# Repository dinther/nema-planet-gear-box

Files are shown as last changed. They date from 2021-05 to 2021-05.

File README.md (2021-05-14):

# nema-planet-gear-box
parametric, silent planet gearbox for 3D print

# Introduction
Yes, yet another 3D printable planet gearbox. For my project I needed a gearbox as flat as I could possibly make it and silent. The result is this gearbox that can measure as thinas 8 mm thick depending on torque requirements and D-shaft design on the motor at hand. The gearbox is stackable where subsequent stacks are even thinner than the first one.

Contrairy to the many well intended 3D printable panet gear solutions out there, this gearbox is mathematically correct. What this means is that not all teeth combinations mesh properly. They can be forced to mesh by adjusting various tolerances but the result would be a wobbly and noisy gearbox. You know the ones.

This gearbox is tried, printed, modified, printed again tested over an over for months with a pile of parts to show for it. But the results are worth it as you can see in the linked video.

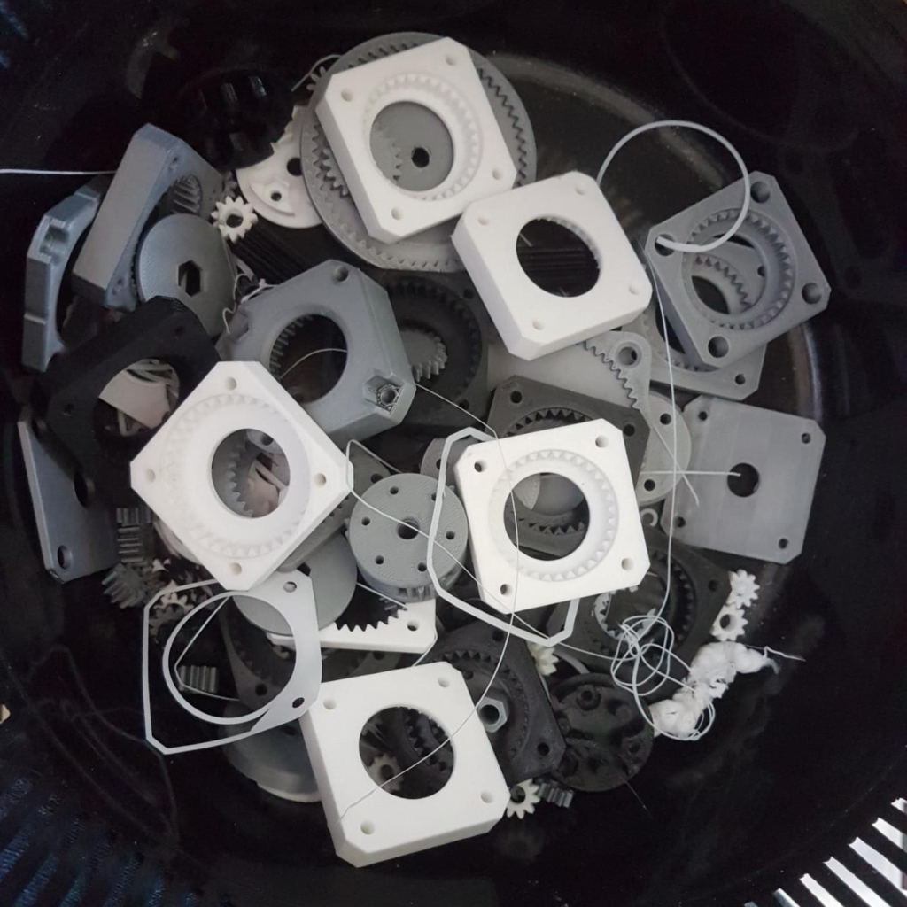
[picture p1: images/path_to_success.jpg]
Path to success

<video width="320" height="240" controls>
  <source src="nema17_quiet_gearbox.mp4" type="video/mp4">
</video>

# Capabilities
This planet gearbox comes in four sizes to match Nema11, Nema14, Nema17, Nema23 and Nema34. It uses 3 planet gears driven by the sun gear in the middle which is attached to the Nema stepper motor. The gearbox can be directly mounted onto the Nema motor face plate and has the same square shape and size as the motor.

All printed tests have been on a 36 teeth annulus, with both sun and planet gears set to 12 teeth. This produces a silent and smooth 1:4 gear ratio.
The following gear ratios have been shown to mesh as well and this applies for any of the above mentioned Nema motors:

Ratio   | Annulus | Sun | Planet | Pitch
--------| ------- | --- | -------| ----- 
2.6     |60       |36   |12      | ?
3.0     |44       |22   |11      | ?
3.15789 |41       |19   |11      | ?
3.3     |42       |18   |12      | ?
3.375   |38       |16   |11      | ?
3.5     |30       |12   | 9      | ?
3.6     |26       |10   | 8      | ?
3.69231 |35       |13   |11      | ?
3.75    |44       |16   |14      | ?
3.8     |42       |15   |13      | ?
4       |27       | 9   | 9      | ?
4       |36       |12   |12      | ?
4       |45       |15   |15      | ?
4.2     |32       |10   |11      | ?
4.25    |39       |12   |13      | ?
4.5     |42       |12   |15      | ?
4.667   |33       | 9   |12      | ?
4.8     |38       |10   |14      | ?
5.4     |44       |10   |17      | ?
6.0     |60       |12   |24      | ?

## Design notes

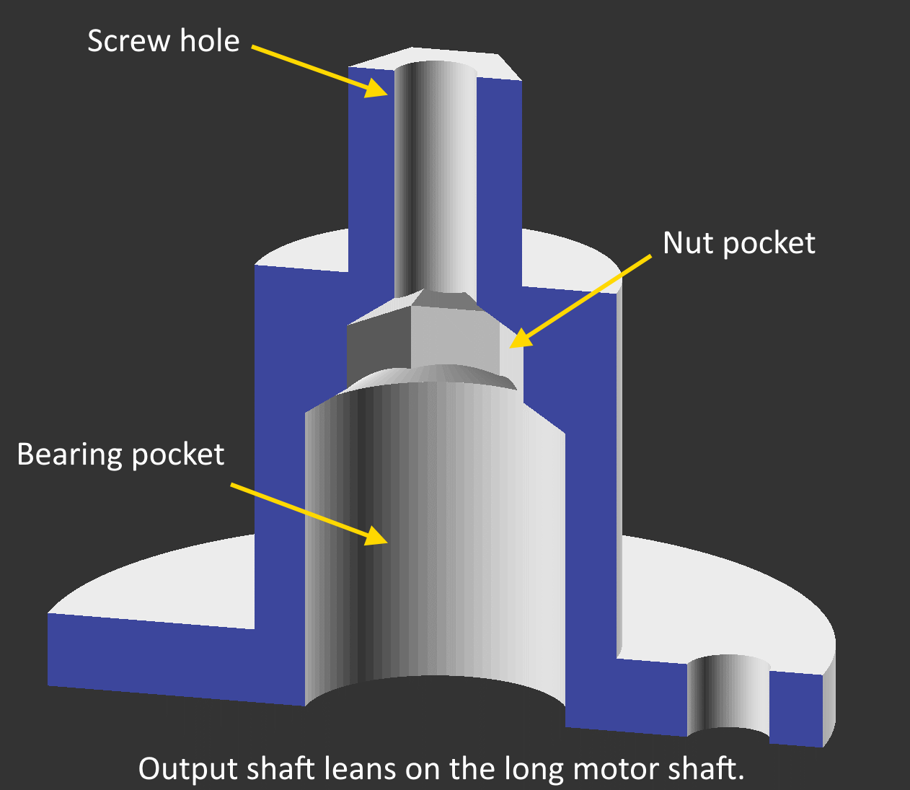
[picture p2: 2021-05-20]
images/cross_section_wheel_shaft_annotated.png

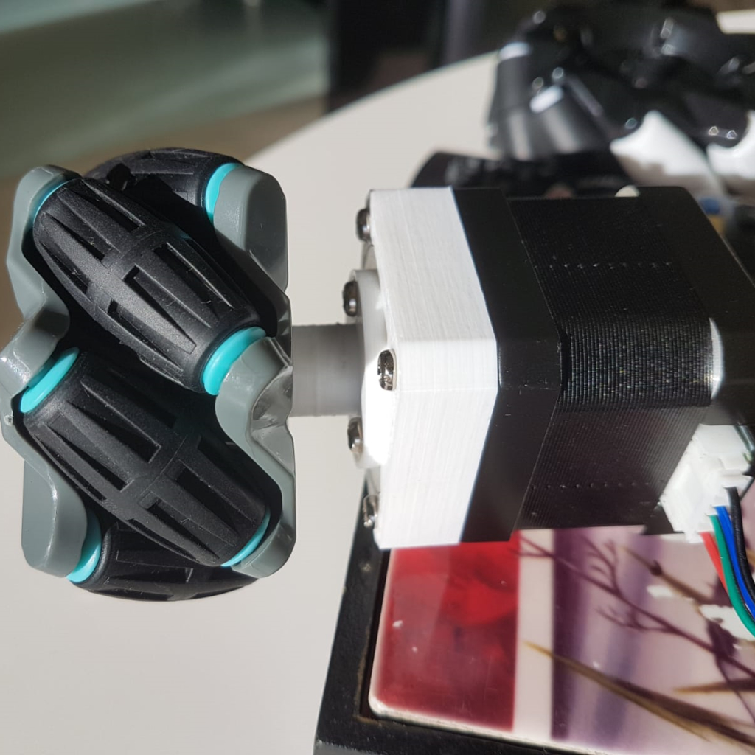
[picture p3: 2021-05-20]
images/gearbox_directly_on_motor.jpg

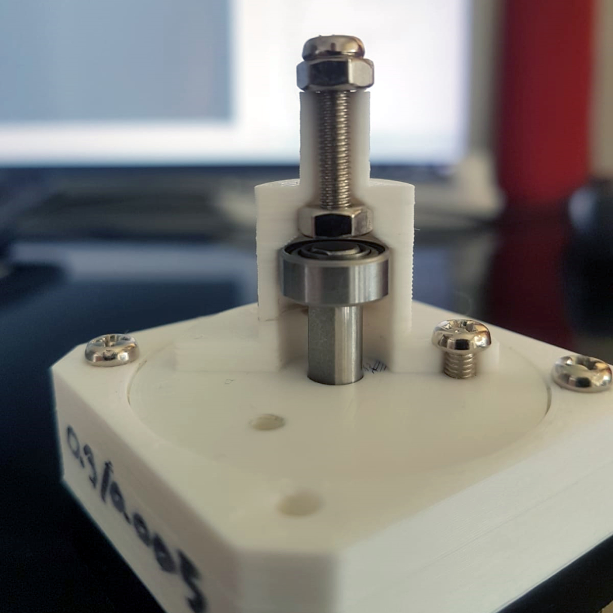
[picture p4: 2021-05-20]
images/cross_section_output_shaft_supported_by_motor_shaft.jpg

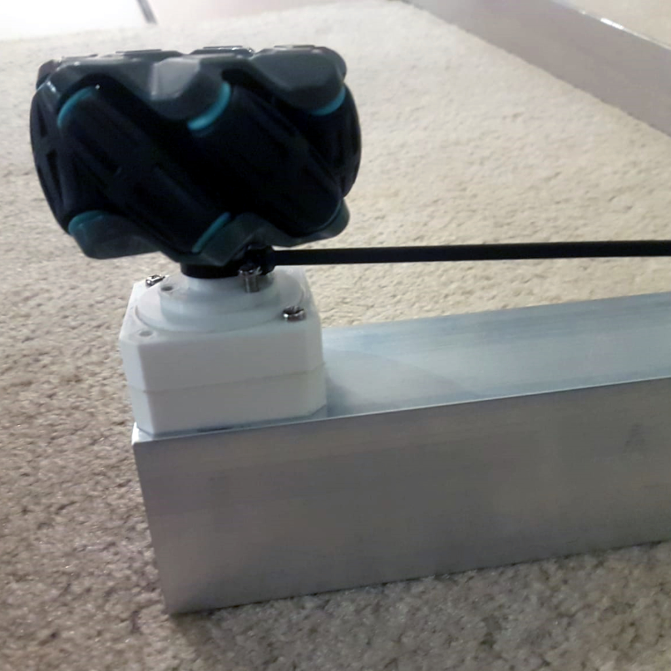
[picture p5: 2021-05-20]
images/two_gearboxes_stacked.jpg

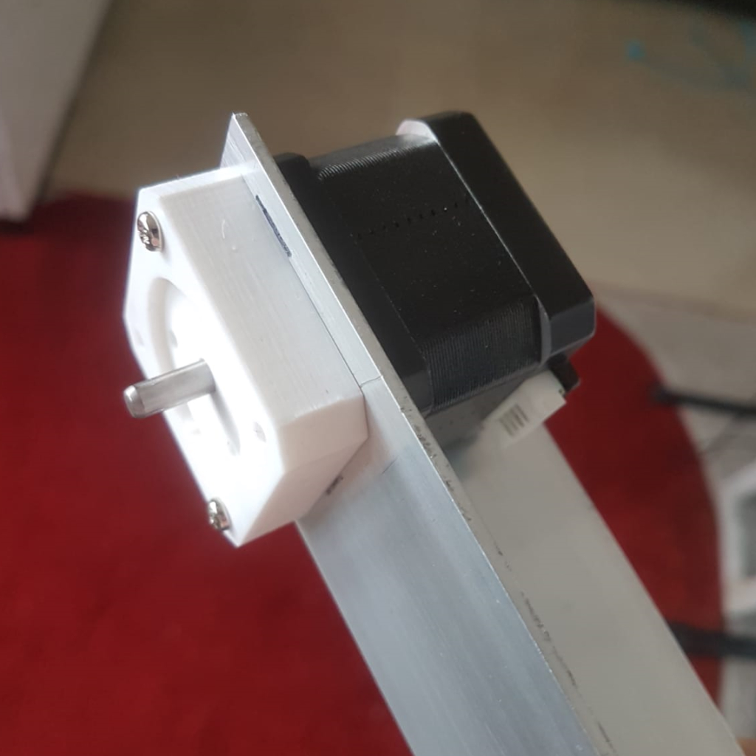
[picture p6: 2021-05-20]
images/gearbox_outside_or_inside.jpg

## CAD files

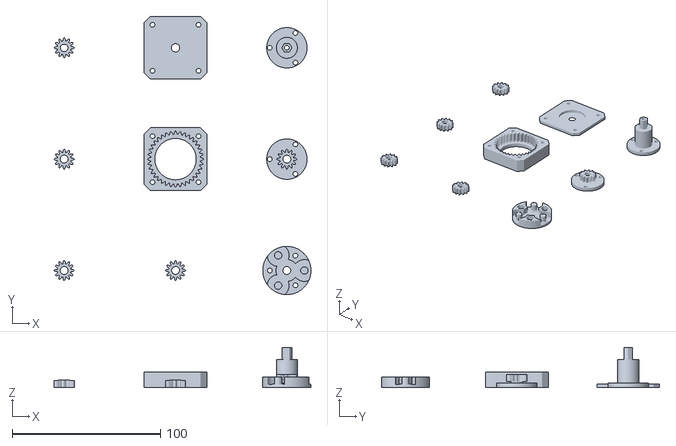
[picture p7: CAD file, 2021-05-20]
stl/gear_box_n17c_361212-25_all.stl
173.1 x 187.4 x 27.1

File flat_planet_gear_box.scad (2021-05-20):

include <./BOSL2/std.scad>
include <./BOSL2/nema_steppers.scad>
include <./BOSL2/gears.scad>

// Super flat planet gearbox for nema motors
// By: Paul van Dinther
//
// For my project I needed a gearbox as flat as I could possibly make it.
// This gearbox measures 11 mm thick and it can be thinner depending on
// the motor plinth and point where the D-shaft starts.
//
// Not all annulus and sun teeth count settings make the teeth mesh
// Easiest way to use:
//
// In the customizer section "View" turn off the following:
//     layout_for_print = false
//     show_cover       = false
//     show_carrier     = false
// Leave the rest set to True
// Next you set the view in OpenSCAD to isometric and select the top view
// That way you can best see if the gears fit nicely.
// If gear teeth overlap it beans that that combo of annulus teeth and sun teeth is not possible
// It is possible to fudge things a bit by changing the gear_backlash value if too tight or too loose.


// settings that work well, ordered by gear ratio:
// ratio Annulus  sun  planet
// 2.6      60    36   12
// 3.0      44    22   11
// 3.15789  41    19   11
// 3.3      42    18   12
// 3.375    38    16   11
// 3.5      30    12    9
// 3.6      26    10    8
// 3.69231  35    13   11
// 3.75     44    16   14
// 3.8      42    15   13
// 4        27     9    9
// 4        36    12   12
// 4        45    15   15
// 4.2      32    10   11
// 4.25     39    12   13
// 4.5      42    12   15
// 4.667    33     9   12
// 4.8      38    10   14
// 5.4      44    10   17
// 6.0      60    12   24
//
//No combinations for Annulus: 28, 29, 31, 34, 37, 40, 43,
//Note: in some case the nut_distance_from_center needs to be adjusted or
//mounting_nuts needs to be turned off in which case there will be a


// Function: nema_motor_shaft_diam()
// Description: Returns the diameter of a NEMA motor shaft of given standard size.
// Arguments:
//   size = The standard NEMA motor size.
function nema_motor_shaft_diam(size) = lookup(size, [
        [11.0, 5.0],
        [14.0, 5.0],
        [17.0, 5.0],
        [23.0, 6.35],
        [34.0, 5], //12.7],
    ]);
    
    
/*[ You Measure ]*/
nema_shaft_length_above_plinth = 21.7;
motor_plinth_to_D_shaft = 3.6;

/*[ General ]*/
sunken_bolt_head_radius = 2.61;
sunken_bolt_head_depth = 2.01;
// Loose fit
planet_gear_shaft_radius_clearance = 0.15;
// Tight fit
sun_gear_shaft_radius_clearance = 0.09;
plinth_sun_gear_clearance = 0.1;

/*[ Plinth base (magenta)]*/
//Set to negative to match motor plinth height
plinth_base_height = -1.01;
plinth_radius_clearance = 0.15;

/*[ Annulus (silver)]*/
nema_size=17; //[11:Nema11, 14:Nema14, 17:Nema17, 23: Nema23,34: Nema34 ]
carrier_cap_recess_height = 2.2;
annulus_teeth_count = 36;
inclusions = 3; //[1: None, 2:Plinth base, 3: Cover]
hole_tolerance = 0.11;

/*[ Cover (red)]*/
//Set to negative to match motor plinth height
cover_height = -1.01;

/*[ Gear parameters sun: yellow planet: blue]*/
sun_teeth_count = 12;
gear_height = 5.5;
gear_backlash = 0.25;
gear_pressure_angle = 28;
gear_shaft_radius = 2.5;
gear_spacer_height = 0.3;

/*[ Carrier (green) ]*/
carrier_cap_height = 2.01;
carrier_radius_tolerance = 0.21;
carrier_height_clearance = 0.1;
carrier_gear_height_clearance = 0.11;
gear_cutout_radius_clearance = 0.5;
hex_nut_pockets = true;
hex_nut_hole_width = 5.99;
nut_distance_from_center = 11.5;
nut_orientation = 30;
mounting_hole_radius = 1.5;

/*[Output shaft (gray)]*/
// Set to negative to match motor plinth height
mounting_plate_height = -1.01;
mounting_plate_bolt_clearance = 0.5;
mounting_plate_radius_clearance = 0.25;
output_shaft_type = 2; //[1: Flat without motor shaft hole, 2: Flat with motor shaft hole, 3: sleeve only, 4: Output shaft on sleeve, 5: output D shaft on sleeve, 6: gear on sleeve ]
//Set to negative to match motor shaft length
output_sleeve_height = -1.01;
output_sleeve_cap_height = 2.01;
output_sleeve_outer_radius = 7.01;
output_sleeve_outer_side_count = 90;
//set to negative to match low friction fit to motor shaft
output_sleeve_inner_radius = -1.01;
output_sleeve_inner_side_count = 90;
//Set to negative to match the other gear heights
output_shaft_height = 10.1;
// Set to negative to match motor shaft
output_shaft_radius = -1.01;
output_shaft_side_count = 90;
output_shaft_bolt_hole_radius = 1.5;
output_gear_teeth_count = 12;
//This clearance allows for a bolt head or a nut to attach things
motor_shaft_to_sleeve_cap_clearance = 2.71;
/*[ Wheel Mounting Plate ]*/
wheel_sleeve_radius = 7.1;
internal_sleeve_radius = 5.2;
hex_size = 5.9;
hex_shaft_height = 8.2;

/*[ View ]*/
layout_for_print = true;
show_plinth_base = true;
show_frame = true;
show_cover = true;
show_carrier = true;
show_sun_gear = true;
show_planet_gears = true;
show_output_shaft = true;
show_wheel_output_shaft = false;
explode = 0; //[0:0.01:1]

$fn = 90;

//useful variables hidden from customizer from here
plinth_height = nema_motor_plinth_height(nema_size);
annulus_pitch_factor = 1 + (gear_backlash / 5 * 0.08); //1.004

//construction values
plinth_radius = nema_motor_plinth_diam(nema_size) / 2;
calc_motor_shaft_radius = nema_motor_shaft_diam(nema_size) / 2;
calc_hole_radius = (nema_motor_screw_size(nema_size) / 2);
calc_cover_height = cover_height < 0? plinth_height : cover_height;
calc_mounting_plate_radius = nut_distance_from_center + calc_hole_radius + hole_tolerance + mounting_plate_bolt_clearance;
calc_mounting_plate_height = mounting_plate_height < 0? plinth_height : mounting_plate_height;
calc_output_shaft_radius = output_shaft_radius < 0? calc_motor_shaft_radius : output_shaft_radius;
total_frame_height = (inclusions == 2? plinth_height : 0) + gear_height + carrier_cap_recess_height + (inclusions == 3? calc_cover_height : 0);
calc_sunken_bolt_head_depth = inclusions != 3? max(min(calc_cover_height - 1, sunken_bolt_head_depth), 0) : max(min(total_frame_height - 1, sunken_bolt_head_depth), 0);

//gear calculations
annulus_outer_radius = min(nema_motor_width(nema_size) / 2 - 1, nema_motor_screw_spacing(nema_size) / 2 * sqrt(2) - calc_hole_radius - hole_tolerance - 1);
gp = (annulus_outer_radius * 2 * PI) / annulus_teeth_count;
annulus_pitch_radius = annulus_outer_radius - gp / 2;
gear_pitch = (annulus_pitch_radius * 2 * PI) / annulus_teeth_count;
ACP = (annulus_pitch_radius*2/annulus_teeth_count) * 180;
planet_teeth_count = round((annulus_pitch_radius * 2 - sun_teeth_count * (ACP / 180)) / 2/(ACP / 180)); //Number of teeth on Planet Gear
ring_outer_radius = outer_radius(teeth = annulus_teeth_count, pitch = gear_pitch * annulus_pitch_factor, interior=true);
ring_root_radius = root_radius(teeth = annulus_teeth_count, pitch = gear_pitch * annulus_pitch_factor);
planet_outer_radius = outer_radius(teeth = planet_teeth_count, pitch = gear_pitch);
planet_pitch_radius = pitch_radius(gear_pitch, planet_teeth_count);
planet_root_radius = root_radius(teeth = planet_teeth_count, pitch = gear_pitch);
planet_spacer_width = min(1.5, (planet_root_radius - calc_motor_shaft_radius) * 0.8);
sun_outer_radius = outer_radius(teeth = sun_teeth_count, pitch = gear_pitch);
sun_pitch_radius = pitch_radius(gear_pitch, sun_teeth_count);
sun_root_radius = root_radius(teeth = sun_teeth_count, pitch = gear_pitch);
sun_spacer_width = min(1.5, (sun_root_radius - calc_motor_shaft_radius) * 0.8);
planet_distance = (annulus_pitch_radius - sun_pitch_radius)/2 + sun_pitch_radius;

echo("__________________________________________________");
echo("\tGear ratio\t\t: ", 1 + annulus_teeth_count / sun_teeth_count);
echo("\tGear pitch\t\t: ", gear_pitch);
echo("\tAnnulus teeth\t\t: ", annulus_teeth_count);
echo("\tAnnulus pitch radius\t: ", annulus_pitch_radius);
echo("\tSun\t\t: ", sun_teeth_count);
echo("\tSun pitch radius\t: ", sun_pitch_radius);
echo("\tSun root radius\t: ", sun_root_radius);
echo("\tSun outer radius\t: ", sun_outer_radius);
echo("\tPlanet\t\t: ", planet_teeth_count);
echo("\tPlanet pitch radius\t: ", planet_pitch_radius);
echo("\tPlanet root radius\t: ", planet_root_radius);
echo("\tTotal height\t\t: ", show_cover? total_frame_height + calc_cover_height : total_frame_height );
echo("__________________________________________________");

module baseHoles(include_shaft_hole = true){
    for(i = [0:2]){
        rotate([0,0,(i*120)-60])
        translate([nut_distance_from_center,0,-50])
        cylinder(h = 100, r = calc_hole_radius + hole_tolerance);
    }
    if (include_shaft_hole){
        translate([0,0,-1])
        cylinder(h = 102, r = calc_motor_shaft_radius + planet_gear_shaft_radius_clearance);
    }
}

module mounting_plate(include_shaft_hole = true){
    difference(){
        cylinder(h = calc_mounting_plate_height, r = calc_mounting_plate_radius, $fn=$fn*2);
        baseHoles(include_shaft_hole);
    }
}
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

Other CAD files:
BOSL2/constants.scad
BOSL2/nema_steppers.scad
BOSL2/phillips_drive.scad
BOSL2/affine.scad
BOSL2/arrays.scad
BOSL2/attachments.scad
BOSL2/beziers.scad
BOSL2/bosl1compat.scad
BOSL2/bottlecaps.scad
BOSL2/bottlecaps_adapters.scad
BOSL2/common.scad
BOSL2/coords.scad
BOSL2/cubetruss.scad
BOSL2/debug.scad
BOSL2/distributors.scad
BOSL2/edges.scad
BOSL2/fnliterals.scad
BOSL2/gears.scad
BOSL2/geometry.scad
BOSL2/hingesnaps.scad
BOSL2/hull.scad
BOSL2/joiners.scad
BOSL2/knurling.scad
BOSL2/linear_bearings.scad
BOSL2/masks.scad
BOSL2/math.scad
BOSL2/metric_screws.scad
BOSL2/modular_hose.scad
BOSL2/mutators.scad
BOSL2/partitions.scad
BOSL2/paths.scad
BOSL2/polyhedra.scad
BOSL2/primitives.scad
BOSL2/quaternions.scad
BOSL2/queues.scad
BOSL2/regions.scad
BOSL2/rounding.scad
BOSL2/screws.scad
BOSL2/shapes.scad
BOSL2/shapes2d.scad
BOSL2/skin.scad
BOSL2/sliders.scad
BOSL2/stacks.scad
BOSL2/std.scad
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
